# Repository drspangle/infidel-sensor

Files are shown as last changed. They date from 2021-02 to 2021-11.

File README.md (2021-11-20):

# Inline Filament Diameter Estimator, Lowcost (InFiDEL)

<p xmlns:dct="http://purl.org/dc/terms/" xmlns:vcard="http://www.w3.org/2001/vcard-rdf/3.0#">
  <a rel="license"
     href="http://creativecommons.org/publicdomain/zero/1.0/">
    
  </a>
  Originally created by Thomas Sanladerer
</p>

*A cheap, yet precise filament diameter sensor, intended to compensate for filament diameter deviations in real-time.*

The InFiDEL is a cheap (< $5) filament diameter sensor intended for use with FDM 3d printers.
The sensor can be calibrated to provide surprisingly precise filament diameter readings in real-time. 
The main idea is to use the sensor to correct for filament diameter deviations while printing.

Based on this proof-of-concept: https://www.youmagine.com/designs/filament-diameter-sensor

Detailed documention for InFiDEL: https://infidel-sensor.readthedocs.io/

## Assembly and Setup
Assembly and Setup Instructions on Youtube (https://www.youtube.com/watch?v=RYgdLPe_T0c)

### Calibration
- Flash board with calibration.ino
- Connect a host via I2C (see provided host-example.ino)
- Insert each calibration drill bit shafts and replace the lookup table entries in driver.ino with your own measurements
  * Measure the actual diameter of the shafts and fill second column
  * Use the host's output *1000 to fill first column
- Finally, flash driver.ino with your values filled out
- Hub should now output exact diameter values

#### Note:
Analog output is currently not enabled in driver.ino (I2C and FAULT pin only)

## BOM

### Printed Parts
1 Block
1 Lever

#### Note:
Parts should preferably be printed in PETG, ABS or ASA as PLA may creep significantly over time.

### Electronics
There are two board variants included in this repository, either can be used to assemble the InFiDEL. 
PCBs and electronic components can be easily ordered via the [Kitspace project page](https://kitspace.org/boards/github.com/drspangle/infidel-sensor/) as it can auto-fill carts and get pricing on PCBs and electronic components from common suppliers.

Choose one:
- SMT control board (which is populated; Gerber files and component specifications are included) 
- THT control board

Also required:

- Suitable programmer for ATTiny85 (eg USBtinyISP)
- 1 SS495A linear hall effect sensor (or comparable)

### Fasteners
- 2 M3x8 screws (eg ISO 4762 M3x8)
- 1 3x24mm pin (eg DIN 7 3x24mm, for mating lever to the block)
- 1 3x16mm pin (eg DIN 7 3x16mm, for roller bearing in lever)
- 1 3x18mm pin (eg DIN 7 3x18mm, for idler bearing in block)
- 6 M3 threaded inserts
- 1 M6x5 or M6x8 grub screw (eg ISO 4026 M6x5, for pre loading spring) 

Pins may be replaced with screws or grubscrews, which may result in decreased precision.

### Other Hardware
- 1 6x2mm magnet (eg N35)
- 4 623 bearings (preferably 623-2Z / 623-ZZ)
- 1 Ballpoint pen spring (or other soft 4mm spring)
- Short length of PTFE tube

### Calibration Accessories
- 1 1.5mm drill bit
- 1 1.7mm or 1.8mm drill bit 
- 1 2mm drill bit
- Calipers for verifying drill bit shaft diameter

Drill bits may be replaced with similar diameters. 
Measured diameter is to be written to firmware lookup table.

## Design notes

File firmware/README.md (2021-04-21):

# Inline Filament Diameter Estimator, Lowcost (InFiDEL) - Firmware

<p xmlns:dct="http://purl.org/dc/terms/" xmlns:vcard="http://www.w3.org/2001/vcard-rdf/3.0#">
  <a rel="license"
     href="http://creativecommons.org/publicdomain/zero/1.0/">
    
  </a>
  Originally created by Thomas Sanladerer
</p>

## Files
| File | Note |
| --- | --- |
| calibration.ino | First test firmware by Thomas Sanladerer, it sends the ADC raw value over I2C, insert some drills of known diameters into the sensor and note the ADC value, then put the values into driver.ino and re compile |
| driver.ino | Code for the sensor, it uses a hardcoded table to convert the ADC to Diameter, and sends 2 bytes over I2C -- no analog out |
| host-example.ino | Reads  the 2 bytes of diameter over I2C, and displays it over the UART, used to test the sensor |
| Host_ee_prog.ino | Code for the Host Arduino, uses bidirectional communication with the sensor and has a simple UART Console to do the calibration and sensor testing |
| Infidel_release_ee.ino | Firmware for the sensor, table in EEPROM, sets values over I2C |

## Setup and Programming 

### Requirements
- Arduino > V1.8.8
- TinyWireS LIbary from https://github.com/nadavmatalon/TinyWireS
- ATtiny85 Board for Arduino from https://github.com/damellis/attiny
- ISP Programmer like Arduino over ISP --> https://www.arduino.cc/en/Tutorial/BuiltInExamples/ArduinoISP
 
Load the code, wire the ISP program to the ISP port on the sensor and program it.

Remember to set the processor to Attiny85.

Tools --> Processor: Attiny85

Tools --> Clock: Internal 1 MHz

Tools --> Burn bootloader to set the fuses

Sketch --> Upload with Programmer

After programming, the LED should flash two times.

## Wiring to the Host Board

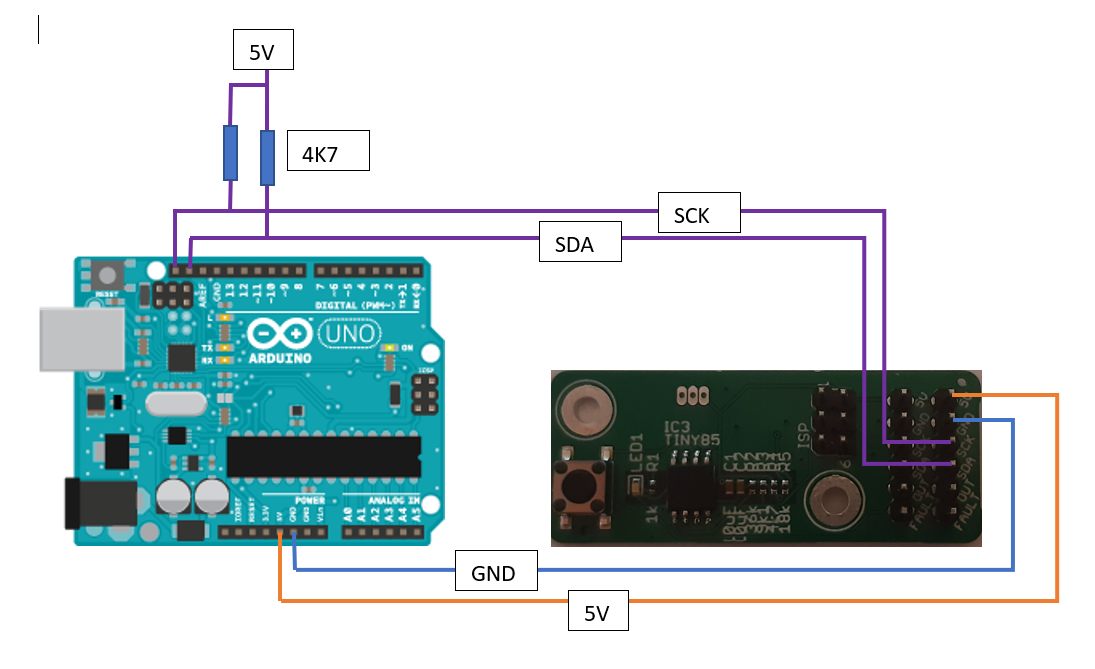
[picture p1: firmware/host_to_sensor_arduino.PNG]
Wire Diagram


Connect the the sensor to the host board, such as an Arduino Uno or Mega.

Program the Host with Host_ee_prog.ino and start the console with 19200 baudrate.

## Console

On start, the following is shown:
```sh
Infidel Sensor Programmer
Scanning...
I2C device found at address 43 
 
Version: 3.12
Table [ADC] [DIA in um]:
00: 0000 / 3000
01: 0619 / 2090
02: 0702 / 1700
03: 0817 / 1400
04: 1000 / 1000
05: 1023 / 0000
Table [DAC min Uout in uV] [DAC max Uout in uV]:
09: 1344 / 2017
Command Input 0 - val / 1 - RAW val / 2 - Version / 3 - Table / 4 - Set Tabel Val / 5 - Ongoing raw read / 6 - sample Mean ADC Val
Command Input 7 - DAC 0 PWW / 8 - DAC 255 PWM

```

| Commands | Note |  Output |
| --- | --- |  --- |
| 0 | Read the Diameter value  |  Diameter [mm]: 2.242 |
| 1 | Read the Diameter + raw ADC Value | Diameter [mm] / [ADC]: 2.242 / RAW: 515 |
| 2 | Read the Version | Version: 1.11 |
| 3 | Read the Diameter Table | Table [idx] [ADC] [DIA in um] |
| 4 | Set the Value in the Table | Input values for Table [IDX],[ADC],[DIA um] like (1,619,2090) |
| 5 | Ongoing reading the ADC raw Value, stop when the command 5 is sent one more time | 
| 6 | Read Meanvalue from Sensor (100 Samples), Display Min / Max / Mean / cnt, used it for Calibration | ADC Mean: 704 / Min: 688 / Max: 713 / Cnt: 100 |
| 7 | Set DAC to PWM 0 --> for check Output Voltage at LOW |
| 8 | Set DAC to PWM 255 --> for check Output Voltage at HIGH |
| h | Show the command list |

## Calibration

Start with the bigger shaft of known diameter (e.g., 2 mm), insert it into the sensor and read the raw ADC value with command "6".
Command "6" determines the mean value over 100 measurements and removes the outliers

```sh
ADC Mean: 704 / Min: 688 / Max: 713 / Cnt: 100
```
Note the ADC value and use the command "4".
The console should show:

```sh
Input values for Table [IDX],[ADC],[DIA um] like (1,619,2090)
Input: 
```

Input this string: `1,503,2000`
Means, Table Index 1 (Command "3"), ADC Val 503, Diameter 3

Repeat this for the next two Ddiameter (1,7mm, 1,4 mm) and write the values to the sensor.

At the end check the settings with Command "3".

```sh
Table [ADC] [DIA in um]:
00: 0001 / 2999
01: 0617 / 2092
02: 0722 / 1711
03: 0816 / 1401
04: 0999 / 1001
05: 1022 / 0001
```

The values are stored in the EEPROM and will load from the EEPROM at the next power up.

If you program the sensor with a new firmware over the ISP the EEPROM will be erased and the sensor will start with default settings.
 
## Calibration with Button (Standalone)

Press the Button at Powerup for 3 sec, if the Calibrationmode start the LED flashes 10 times
The sensor sends an analog signal to Pin 5 [OUT].

* Step 1, Led Flash 1 Times
	*   Insert Drill with 1,4mm
	*   Wait a short Time, 1-2 sec
	*   Press the Button for 1 sec
	*   The Led light for 2 sec, the Sensor is getting 100 Samples from the ADC 
	*   If the messure is Ok the Led flash fast
	*   Remove the drill an press the Button
*   Step 2 Led flashes 2 Times (1,7mm Drill)
    *   Insert the Drill 1,7mm and repeat Step 1
*   Step 3, Led flash 3 times (2mm Drill)
	*   Insert the Drill with 2mm and repeat Step 1

The Calibration is done

## Analog Output
 
The sensor sends an analog signal to Pin 5 [OUT].

The range goes from 1.42 VDC to 2.14 VDC .
The voltage is the analog for the diameter: 1.73V is equal to 1.73mm diameter.

## Calibrate the Analog Output

Connect a Multimeter to GND and OUT.
The Analog Output depend on the VCC Voltage, so make the Calibration when the Sensor is connected to the Printerboard
and not to the unstable USB Port.

* Set with the command "7" the PWM to LOW, meassure the Voltage on Analog OUT and note it (like 1,344 V)
* Set with the command "8" the PWM to HIGH, meassure the Voltage on Analog OUT and note it (like 2,017 V)

Set with the command "4" the table Value for Index 9 (Calibration Values for DAC)
IDX 9 then LOW Voltage and the HIGH Voltage --> like: 9,1344,2017

Check the table with command "3".
The Values are stored in the EEPROM for the next Start

## Fault Pin

The fault pin is high when the diameter is bigger than 3mm and smaller than 1.5mm.
This indicates that the sensor is outside of the normal working range.

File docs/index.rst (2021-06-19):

.. Inline Filament Diameter Estimator, Lowcost (InFiDEL) documentation master file, created by
   sphinx-quickstart on Sat May 15 21:44:02 2021.
   You can adapt this file completely to your liking, but it should at least
   contain the root `toctree` directive.

Welcome to InFiDEL's documentation!
=================================================================================

*A cheap, yet precise filament diameter sensor, intended to compensate for filament diameter deviations in real-time.*

The InFiDEL is a cheap (< $5) filament diameter sensor intended for use with FDM 3d printers.
The sensor can be calibrated to provide surprisingly precise filament diameter readings in real-time.
The main idea is to use the sensor to correct for filament diameter deviations while printing.

Based on this proof-of-concept: https://www.youmagine.com/designs/filament-diameter-sensor

.. toctree::
   :maxdepth: 2
   :caption: Contents:

   license
   bom
   assembly_and_setup

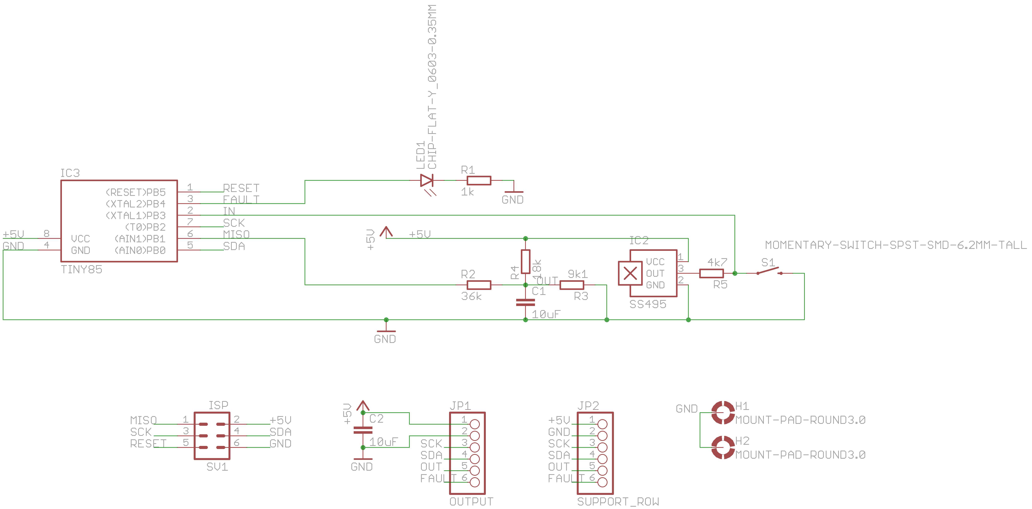
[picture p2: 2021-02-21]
electrical/smt/EAGLE/SMT schematic.png

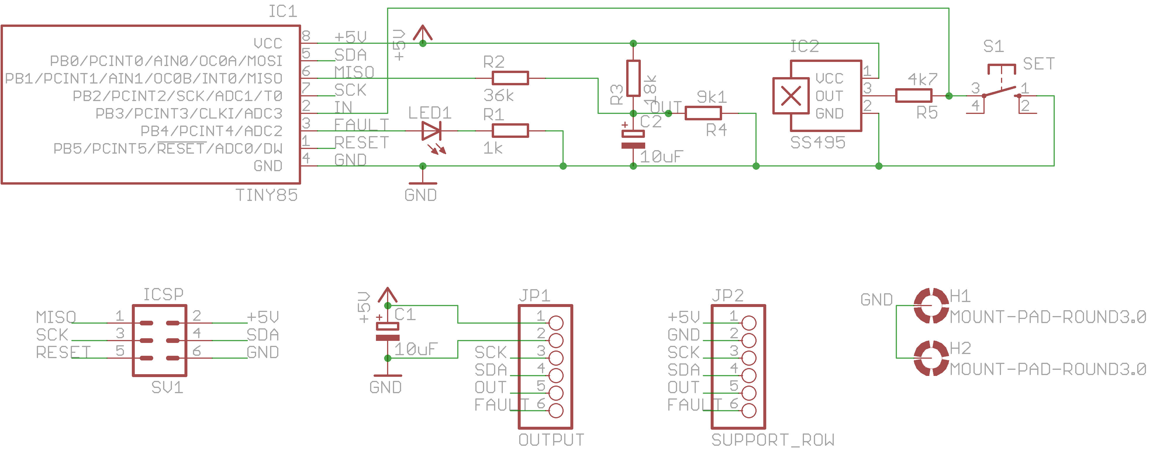
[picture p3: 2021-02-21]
electrical/tht/EAGLE/THT schematic.png

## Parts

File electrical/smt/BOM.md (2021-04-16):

Comment | QTY | Designator | Footprint | Mouser #
--------|-----|------------|-----------|------------
1k Resistor | 1 | R1 | R0402 | [667-ERA-2VEB1001X](https://www.mouser.com/ProductDetail/Panasonic/ERA-2VEB1001X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)
4k7 Resistor| 1 | R5 | R0402 | [667-ERA-2VEB4701X](https://www.mouser.com/ProductDetail/Panasonic/ERA-2VEB4701X?qs=sGAEpiMZZMtlubZbdhIBIFX24rZb7BVEojE2B5%2FPiTs=)
9k1 Resistor|  1 |R3 | R0402 | [667-ERJ-2RHD9101X](https://www.mouser.com/ProductDetail/Panasonic/ERJ-2RHD9101X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)
10uF Capacitor| 2 | C1 C2 | C0402 | [81-GRM155R60J106ME7D](https://www.mouser.com/ProductDetail/Murata-Electronics/GRM155R60J106ME47D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)
18k Resistor|  1 |R4 | R0402 | [667-ERA-2AEB183X](https://www.mouser.com/ProductDetail/Panasonic/ERA-2AEB183X?qs=sGAEpiMZZMtlubZbdhIBILRDuhBknqQkigW4TZMnrhA%3D)
36k Resistor|  1 |R2 | R0402 | [667-ERA-2ARB363X](https://www.mouser.com/ProductDetail/Panasonic/ERA-2ARB363X?qs=sGAEpiMZZMtlubZbdhIBIAI3Iw0L1RezAP9RFTfVAPU%3D)
LED | 1 | LED1 | LEDC1608X35N_FLAT-Y | [604-AA1608SURSK](https://www.mouser.com/ProductDetail/Kingbright/AA1608SURSK?qs=eP2BKZSCXI6pqonvuMmTFg%3D%3D)
Momentary Switch| 1 | S1 | TACTILE_SWITCH_SMD_6.2MM_TALL | [642-ADTSM63NVTR](https://www.mouser.com/ProductDetail/Apem/ADTSM63NVTR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)
ATTINY85 | 1 | IC3 | SOIC8 | [556-ATTINY85V10SU](https://www.mouser.com/ProductDetail/Microchip-Technology-Atmel/ATTINY85V-10SU?qs=8jWQYweyg6NQ5xH6egcL8w%3D%3D)
SS495A Linear Hall Sensor | 1 | - | TO-92-Flat-3 | [785-SS495A](https://www.mouser.com/ProductDetail/Honeywell/SS495A?qs=%2Ffq2y7sSKcKEzWT94S3drA%3D%3D)
ISP PinHeader 2x3 | 1 | ISP | Pin Header | [649-1012938190601BLF](https://www.mouser.de/ProductDetail/Amphenol-FCI/10129381-906001BLF?qs=0lQeLiL1qyZMxGRnx95Mzg%3D%3D)
I2C Header 1x6 | 2 | - | Pin Header | [649-78511-406](https://www.mouser.de/ProductDetail/Amphenol-FCI/78511-406?qs=44C8ns5dLY9MkbPan6dMVA%3D%3D)

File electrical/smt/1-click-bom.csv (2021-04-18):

References | Qty | Description | Mouser
R1 | 1 | 1k Resistor R0402 | 667-ERA-2VEB1001X
R5 | 1 | 4k7 Resistor R0402 | 667-ERA-2VEB4701X
R3 | 1 | 9k1 Resistor R0402 | 667-ERJ-2RHD9101X
C1 C2 | 2 | 10uF Capacitor C0402 | 81-GRM155R60J106ME7D
R4 | 1 | 18k Resistor R0402 | 667-ERA-2AEB183X
R2 | 1 | 36k Resistor R0402 | 667-ERA-2ARB363X
LED1 | 1 | LED LEDC1608X35N_FLAT-Y | 604-AA1608SURSK
S1 | 1 | Momentary Switch TACTILE_SWITCH_SMD_6.2MM_TALL | 642-ADTSM63NVTR
IC3 | 1 | ATTINY85 SOIC8 | 556-ATTINY85V10SU
- | 1 | SS495A Linear Hall Sensor TO-92-Flat-3 | 785-SS495A
ISP | 1 | ISP PinHeader 2x3 Pin Header | 649-1012938190601BLF
- | 2 | I2C Header 1x6 Pin Header | 649-78511-406

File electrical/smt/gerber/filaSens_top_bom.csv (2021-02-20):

Comment | Designator | Footprint | LCSC Part #
1k | R1 | R0402
4k7 | R5 | R0402
9k1 | R3 | R0402
10uF | C1 C2 | C0402
18k | R4 | R0402
36k | R2 | R0402
CHIP-FLAT-Y_0603-0.35MM | LED1 | LEDC1608X35N_FLAT-Y
MOMENTARY-SWITCH-SPST-SMD-6.2MM-TALL | S1 | TACTILE_SWITCH_SMD_6.2MM_TALL
TINY85 | IC3 | SOIC8

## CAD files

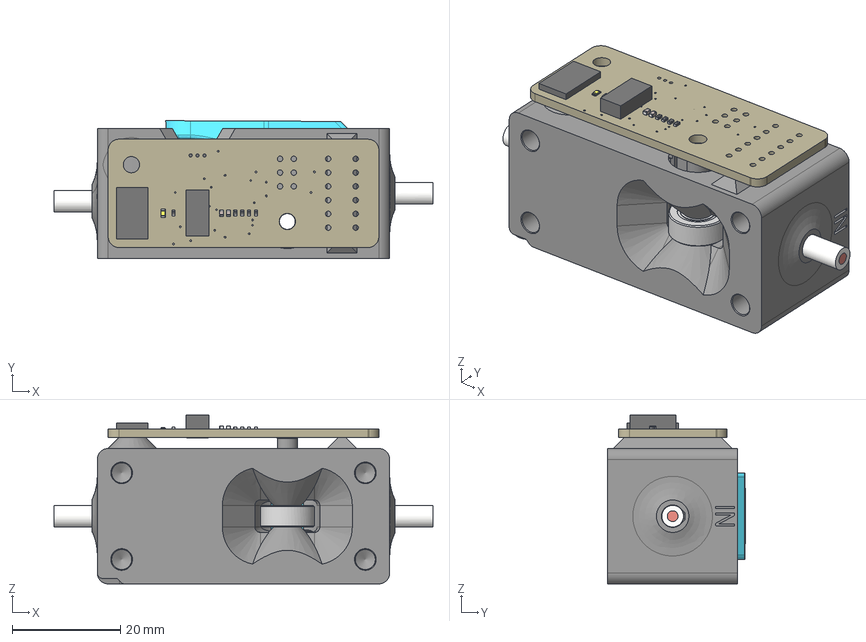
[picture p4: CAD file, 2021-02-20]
mechanical/InFiDEL_release.step
70.0 x 25.4 x 31.2 mm
LeverNew
7804K128 (1)
SpringPlunger
Filament
PTFE (1)
BlockClearance
Board
TACTILE_SWITCH_SMD_6.2MM_TALL
SIP3-UA
SOIC8
C0402 x 2
R0402 x 5

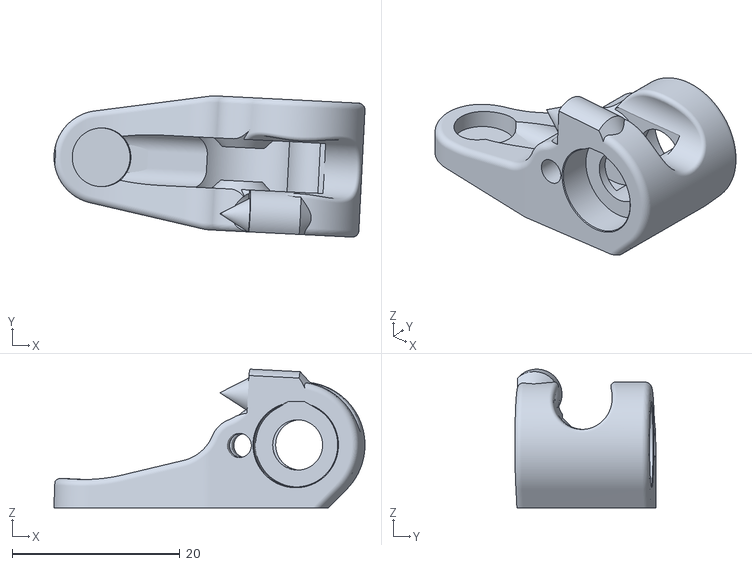
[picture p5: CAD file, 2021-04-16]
mechanical/stl/Lever.stl
37.1 x 16.8 x 16.5

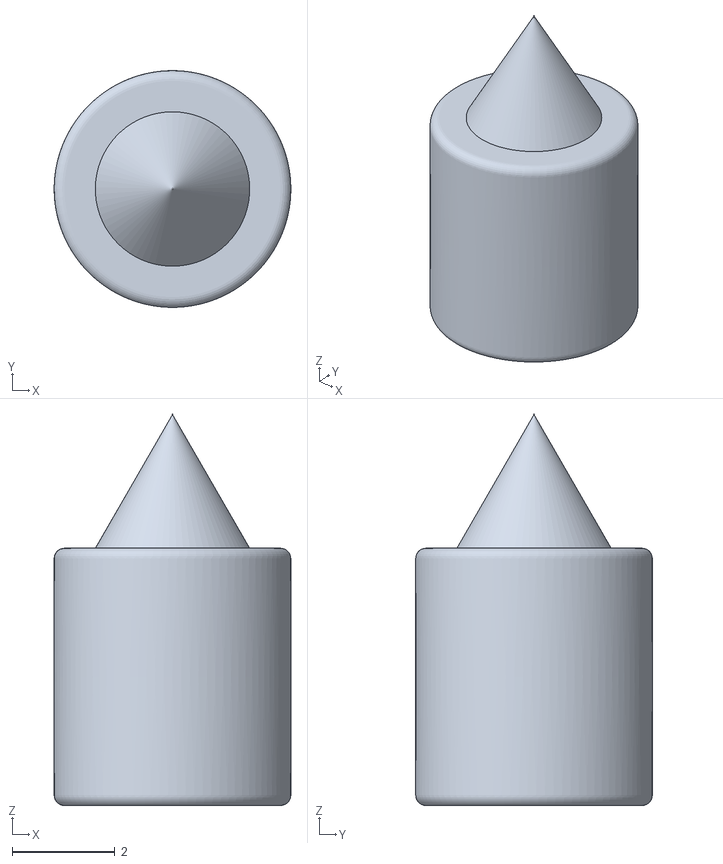
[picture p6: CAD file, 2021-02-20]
mechanical/stl/SpringPlunger.stl
4.60 x 4.60 x 7.60

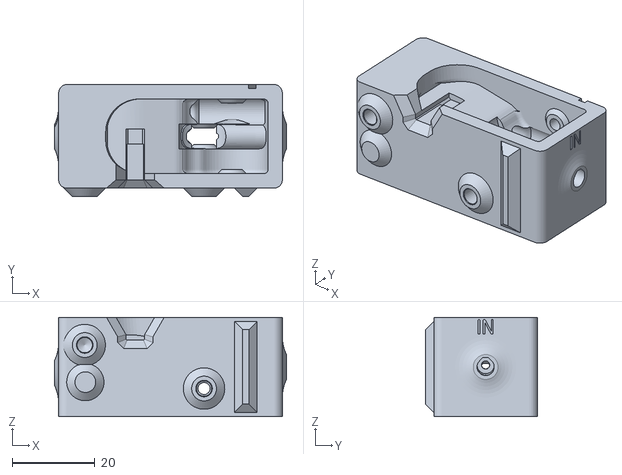
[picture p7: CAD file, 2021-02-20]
mechanical/stl/Block.stl
56.0 x 27.0 x 24.0

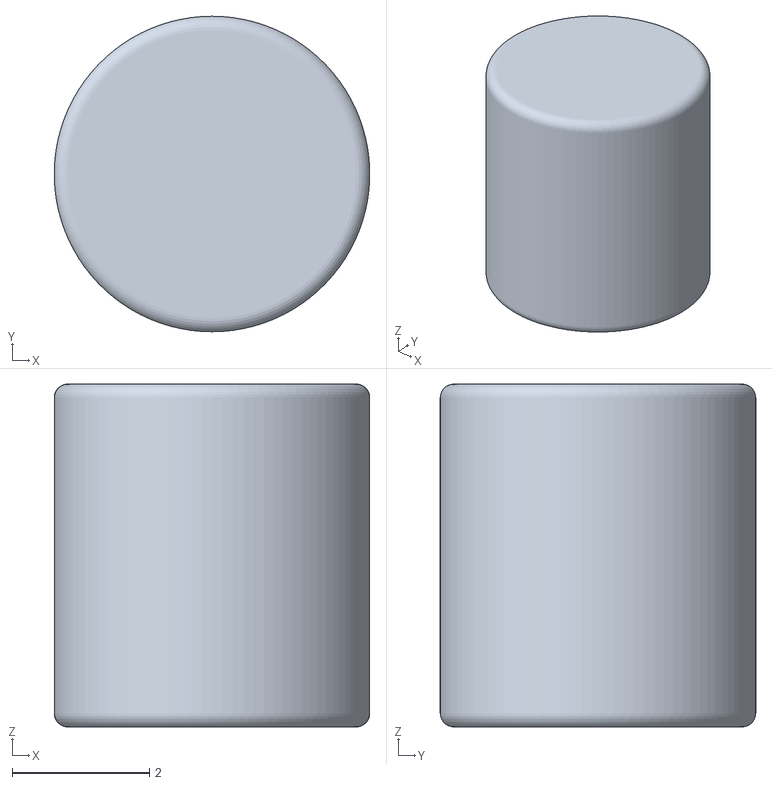
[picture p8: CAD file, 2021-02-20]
mechanical/stl/SpringPlungerExtender.stl
4.60 x 4.60 x 5.00

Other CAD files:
mechanical/LeverDB.f3d

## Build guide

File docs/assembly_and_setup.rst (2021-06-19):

Assembly and setup
==================

Assembly and Setup Instructions on Youtube_

Calibration
-----------
- Flash board with calibration.ino
- Connect a host via I2C (see provided host-example.ino)
- Insert each calibration drill bit shafts and replace the lookup table entries in driver.ino with your own measurements

  * Measure the actual diameter of the shafts and fill second column
  * Use the host's output multiplied by 1000 to fill first column

- Finally, flash driver.ino with your values filled out
- Hub should now output exact diameter values

    Note: Analog output is currently not enabled in driver.ino (I2C and FAULT pin only)


.. _Image: https://www.youtube.com/watch?v=RYgdLPe_T0c

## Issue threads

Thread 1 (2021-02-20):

Choosing an appropriate license

drspangle, 2021-02-20:
It's not clear what license that Thomas Sanladerer intended for this project, he just says it's "all free". We should check to see what he was actually intending -- perhaps it's a CC share-alike license or something.

imitation, 2021-02-20:
"All free" literally means "CC-0 / PD / no rights reserved" in this case. Use in any and every way you deem appropriate - no attribution required (though appreciated).
Allowed use also includes sharing and using any of provided files under a different license.

drspangle, 2021-02-21:
Added LICENSE, fixed in 5d8666c1a287c430bc7336bd76a3391ac569ba7b.

Closed 2021-02-21.

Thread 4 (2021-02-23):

Improve Calibration Procedure - User Feedback

drspangle, 2021-02-23:
Right now, the calibration procedure totally opaque with essentially no user feedback. It would be great if the calibration procedure for the sensor incorporated flashing LEDs to alert the user to the current state of the calibration process. There should be some sort of way to signal the following states:

1. Calibration in progress, insert pin
2. Reinsert pin/retry
3. Calibration stage success, insert next pin
4. Error

Each of the "flash codes" for these states should be documented and the calibration procedure revised.

blurfl, 2021-02-28:
How about adding an I2C display?

drspangle, 2021-02-28:
Nothing wrong with this idea, but it could potentially raise the BOM cost significantly. At the very least, it will require changes to the PCB design and layout. Since calibration shouldn't be happening very often, it might be fine to stick with flash codes for now, since there are only 4 states.

drspangle, 2021-03-05:
It looks like in #8 there was an I2C interface implemented, though I'm not sure how it works and haven't tested it yet. Perhaps there is some potential to do this calibration by connecting to a remote serial console and doing the calibration interactively through that.

blurfl, 2021-03-05:
#8 does set up a serial user interface on the Arduino host, with a 2-way communication to the ATTiny85.

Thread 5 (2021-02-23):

Improve Calibration Procedure - Anomaly Detection

drspangle, 2021-02-23:
Right now, the calibration procedure relies on assumed good measurements for each of the pins of known diameter. A better approach would use repeated measures, then taking the average of these measurements. However, it's possible that erroneous values can creep into the calculations based on the precision of the sensor, and this would drastically affect the operational accuracy. The repeated measures should be combined with a statistical test to ensure that calibration measures are within a certain confidence interval of the likely "population" average, and if they aren't, they should be rejected.

This issue ties in with #4 as it will be necessary to incorporate user feedback in order for the state of the system to be apparent to the user.

The theory of operation and statistical test(s) used should be documented.

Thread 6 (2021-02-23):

Real-Time Measurement Error and Anomaly Detection

drspangle, 2021-02-23:
The micro-controller built in to the sensor has the capability of making the readout smarter than it currently is. While filtering the analog signal from the hall effect sensor certainly helps to minimize the likelihood of extreme outliers with high variance during real-time measurement, it would be nice if there were also built-in tests to determine if there are likely measurement errors or anomalies detected during real-time measurements.

This approach would likely need to rely on certain assumptions, such as the filament being within a certain tolerable spec -- this is likely a safe assumption (using conservative values) as most printers will start to exhibit defective prints in the event that the filament is suddenly out of spec by a huge amount.

The approach to error and anomaly detection is largely dependent on the feed rate (which is unknown to the sensor) and the sensor polling rate (which can be configured).

Errors should be triggered whenever the measurements are (based on statistical tests or otherwise) likely to be far outside the average, perhaps by a configurable threshold (two standard deviations would seem like a very reasonable default). Obviously errors should also be triggered if the filament diameter is detected to be greater than the diameter of the bowden tubes downstream from the sensor (should be configurable), and if the filament is detected to have run out (zero diameter, perhaps over a configurable period of time).

Errors should not be triggered during the following circumstances, as they are the whole point of having the sensor in the first place (assuming otherwise fairly smooth transitions between variances in filament thickness):
- When the filament suddenly gets thicker (as long as it's not so thick there would be a clear problem getting it through the tube), which can happen with filament joiners. This might possibly be an extremely rare condition.
- When the filament suddenly gets thinner (for example, if it has been ground down upstream like in the case of a previous MMU2 loading/unloading failure) the sensor should be capable of detecting this difference and allowing adaptation to the print without failure.

deezums, 2021-03-24:
I agree, and think it might be possible to get the width sensor a feedrate off the signal to the stepper driver. That ought to be able to be used to catch outliers, plus it might be useful for a jam sensor as well.

I've been trying to think of a way to fit a magnetic encoder to the idler bearing, and think tape player pinch rollers might work, around the right size and might be accurate enough to be useful. Although, I think anything I can come up with to fix the idler to the new driven axle shaft would have enough runout to make it unusable as an accurate width sensor, or at least requiring some ridiculous mapping or something. You ought to be able to save a print near instantly on a jam then, plus with a little oled you could track usage and other stats.

I might order a few rubber pinch rollers from ali and see if they might shrink fit on a dowel or something and if they are still decently round, if they'd be hard enough to not deform, and if they'd be able to keep traction...

Outside getting a custom one piece axle made, I'm all ears for ideas for a friction driven idler/axle you could attach a magnet to!

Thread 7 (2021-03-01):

Which TinyWireS library to use

blurfl, 2021-03-01:
calibration.ino and driver.ino both use calls to TinyWireS.write() to send data, but I haven't found a version of the TinyWireS library that includes a write() function instead of send(). Is there a particular library version needed here? Changing .write to .send looks proper and compiles, but I'm not able to test that it works properly.

drspangle, 2021-03-02:
I can't say for sure what the correct library is here as I've yet to construct a prototype for testing myself. If you can show that this works with that change, I strongly encourage a PR which I'll accept expeditiously.

midopple, 2021-03-05:
Hi,
i use this TinyWireS libary

https://github.com/nadavmatalon/TinyWireS

drspangle, 2021-03-05:
@blurfl is the library which @midopple linked to the same as the one you attempted to use?

blurfl, 2021-03-05:
Well found, @midopple. I had not seen this library, but it seems very complete and uses the Arduino Write library's write() approach used by the Arduino host (see Host_ee_prog.ino in #8 for instance). It uses the MIT license, not sure how that meshes with the rest of the project - IANAL.
There would be a benefit to adding the library you settle on to this project 😉

drspangle, 2021-04-24:
It seems like we've settled on the one that @midopple is using, at least in the alternate firmware he's got in here. I think this can be closed now.

Closed 2021-04-24.

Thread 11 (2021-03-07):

JLCPCB makes it look like the pick and place locations are incorrect in the current CPL file

darraghbr, 2021-03-07:
If you go through the order process with JLCPCB the resulting pick and place locations are incorrect.

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

JLCPCB will still accept the files and it should work properly, they go through a checking process where they will adjust the positions by hand.

drspangle, 2021-03-07:
So is the issue that the pad placement for the IC3 chip and the other SMD component is incorrect, or is there a deeper issue here? I'm not seeing precisely what the issue is. Does this screenshot come from JLCPCB's design checker?

darraghbr, 2021-03-07:
I think it's a JLC issue, I've checked and double checked the positions and it just seems the presence of the switch in the CPL file breaks everything.

blurfl, 2021-03-07:
We shouldn't modify our BOM to work around one vendor's internal issue. They correct for it when they review the order.

midopple, 2021-03-08:
I had the same problem with JLCPCB, after contacting support I was told that this is due to the web preview and is still being checked before the production process.

electrickery, 2021-03-20:
My boards arrives some days ago and the components are all at the right places. Haven't started and programmed the board yet.

coelholm, 2021-04-09:
I saw same issue. It is an issue with JLCPCB web preview. I have tried to correct placement position of each component one by one (It was looking fine), but when I got to the last component, everything looked "misaligned" again, so I decided to use original file and my boards are perfect.

drspangle, 2021-04-16:
It seems like this isn't actually an issue, rather is a problem on JLCPCB's end. I'll close this now.

Closed 2021-04-16.

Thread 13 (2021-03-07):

Holes for heat set inserts incorrect size

darraghbr, 2021-03-07:
Let me preface this with the fact that I've not used heat set inserts, so I don't know how sensitive they are to diameter changes.

The holes in the current design are 3.7 mm diameter with a short countersink out to 4 mm. The manufacturers specs for M3 inserts state the hole should be 4 mm.

Does the current design work fine or should the hole sizes be changed? 0.3 mm is not much but is it the difference between a part cracking or not?

drspangle, 2021-03-07:
This is a valid issue but it depends on the material, and also depends on which kind of heat inserts you use. If you use the cheapo ones which are essentially spool shaped, and if you use a material like PETG, having this extra bit of material can help. With PLA this might not be the case.

I think this would be a good issue to keep around, especially if people have issues with printing or assembly.

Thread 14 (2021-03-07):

No mention of spring pre tensioning hardware

darraghbr, 2021-03-07:
I believe there is a missing item on the hardware BOM, I believe there should be an M5 grub screw or the like to pre load the spring in the body of the sensor.

drspangle, 2021-03-07:
I believe you are correct. Tom originally specified that he used a grub screw in his video but I don't know what was specified. Can you verify that an M5 grub screw works, and if so, can you recommend/specify a specific one?

darraghbr, 2021-03-07:
>
>
> I believe you are correct. Tom originally specified that he used a grub screw in his video but I don't know what was specified. Can you verify that an M5 grub screw works, and if so, can you recommend/specify a specific one?

An M5 grub screw definitely does work, and either of the standard sizes (5 or 8 mm long) will work fine.

drspangle, 2021-03-07:
Great! This should definitely get added to the BOM. If you want to create a PR to add this I will review and accept it expeditiously. Nice catch on this one.

drspangle, 2021-03-07:
Fixed in #16.

Closed 2021-03-07.

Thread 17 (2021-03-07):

Investigate the use of the DRV5053 sensor

darraghbr, 2021-03-07:
In place of the SS495A sensor we could instead use a comparable TI part, namely the DRV5053. Pros of the DRV5053 are it is significantly less expensive (less than half the cost) for a similar spec part, they are pin compatible.

I have prototyped the circuit on a breadboard and tested side by side the SS495A sensor and the DRV5053, below is the waveform generated by the two sensors, the DRV is on the left and the SS495A is on the right, as you can see the output is much higher from the SS495.

The polarity is reversed between the sensors, but in theory you just have to install the magnet in the other way around.

I checked it using a magnet on which I marked a side and offered it up to the 2 sensors.

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

Do people think the lower response and reversal of polarity will be an issue?

Below is the breadboard set up for reference.

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

drspangle, 2021-03-07:
The inverted polarity shouldn't be an issue, but I'm wondering about the response time. Do you have a rough idea of what the expected (reliable) sampling rate would be given the small measurement tolerance?

darraghbr, 2021-03-07:
The SS495A datasheets state a response time of 3 μs and the DRV state a typical of 13 μs and a max of 25 μs. I believe either one is appropriate. In terms of sampling rate I'm not sure, but the DRV sensor has a much more detailed application note around designing RC filters to achieve an appropriate bandwidth.

Ultimately it comes down to the filament, it would be interesting to see what sort of frequencies the variations in filament occur at. Can you detect mains switching frequency in the diameter of filament? Of course it wouldn't be at the same frequency unless your feedrate is the same as the original extruder.... Something to keep me awake at night...

blurfl, 2021-03-08:
The reduced response of the DRV5053 is certainly an issue. We're measuring very small differences in movements of the magnet and the chart makes it look like the SS495A has more than four times the full range.

darraghbr, 2021-03-08:
The sensors are closer to one another than you might think, in terms of linear range the DRV sensor beats the SS495 (only by 6 mT but there we are)

Because we are going through a calibration routine I suspect it won't matter, and because we are in a fairly loosely coupled system (lets face it the extruder of a printer can't respond at the rates we are talking about here) I suspect it's all in the weeds.

  | SS495A | DRV5053OA
-- | -- | --
Limits (mT) | 67 | 73
Linearity (%) | 1 | 1
Sensitivity (mV/mT) | 31.25 | 11
Output delay time (μs) | 3 | 13

blurfl, 2021-03-08:
The sensitivity value of the SS495A is more than three times that of the DRV5030A. That’s a lot. We won’t be affected by the limit, we’re working with a small magnet. Our interest is how much the signal changes for a small change in mT.

drspangle, 2021-03-08:
I must admit that as a software guy, the physics and electrical engineering behind the final determination of whether this change will be a problem is increasingly beyond my expertise. However, I would like to offer two things.

First, maybe it would be worth reaching out to Tom to see if he had considered using this alternative sensor, perhaps he has some knowledge or did some tests on this.

Second, it might be worth considering this change in terms of the maximum sensitivity per time unit, rather than overall sensitivity or maximum frequency of a reliable sample in ideal conditions. If we take this approach, it would be more practical to be able to calculate the maximum detectable deviation for a given feedrate, and we can also determine whether this detectable deviation is within an acceptable spec over a number of observations. This is very much related to what I had in mind for #5.

darraghbr, 2021-03-08:
You say we are working with a small magnet, they are quite potent and are quite close to the sensor. Do you know for a fact that we are within the linear region for the sensor?

darraghbr, 2021-03-08:
There are also other SKUs of the DRV5053, including ones with significantly higher sensitivity, in the realm of 90 mV/mT, but they become saturated at much lower levels.

darraghbr, 2021-03-08:
It would be interesting to see what the raw values shake out to be during the calibration process.

blurfl, 2021-03-08:
Maximum sensitivity per time unit would be a function of sensitivity and output delay time. In a device that
The difference in cost here is very small -  these are not expensive parts. The cost of shipping for either one will  be much more than the cost of the part. The sensor in a sensing circuit isn't the best place to cost engineer.

A bigger cost saving might be to use a RPi pico ($4) instead of the custom PCB. Faster, on-board data storage, serial IO as well as I2C, available without custom manufacture.

drspangle, 2021-03-08:
> A bigger cost saving might be to use a RPi pico ($4) instead of the custom PCB. Faster, on-board data storage, serial IO as well as I2C, available without custom manufacture.

While this is true, this is both a substantial change to the hardware design and also a total redo of the firmware (including a shift to a different development environment and language). I'm not sure whether this is a good idea or not at this stage. There is also the potential for a shortfall in available volume of parts.

All of this is a useful discussion, so let's keep hashing this out until we arrive at a practical answer. The goal is to keep the cost as low as possible, but there is an obvious multi-objective trade-off between cost, manufacturability/availability, and utility. It is totally unclear to me what the impact is on these objectives with each of these proposed changes right now.

blurfl, 2021-03-08:
> a substantial change to the hardware design and also a total redo of the firmware

That's a fact. Probably better as a fork. It does work a treat, though 😁.

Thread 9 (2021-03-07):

The lever part has some thin walls that make it almost unprintable

darraghbr, 2021-03-07:
The walls that the bearings locate to are extraordinarily thin, so thin in fact that they are basically unprintable with a normal FDM printer with a 0.4mm nozzle. Even with a 0.25mm nozzle I don't think these details are resolvable in a suitable material ASA, PETG as specified by the original designer.

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

Whereas the solid part should look like:

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

Looking in the CAD the inner and outer faces appear to be intersecting, which will absolutely make any printer sad, as it's trying to print something that is infinitely thin.

drspangle, 2021-03-07:
Is there any likelihood that this was done on purpose?

deezums, 2021-03-24:
The closer the fulcrum is to the fixed pivot the larger the movement at the end of the lever, in other words it's probably on purpose. Nothing about that is unprintable, nor would it be mechanically unsound.  Both bearings and the axle have plenty of material constraining them.

darraghbr, 2021-03-24:
That is not at all what we are talking about or what I have changed in the linked PR.

drspangle, 2021-03-24:
@darraghbr I apologize for the confusion, could you help everyone understand a little better what you are trying to address, versus what @deezums has raised?

darraghbr, 2021-03-24:
In the original CAD there is an infinitely thin wall behind the upper part of the bearing seat, which no printer will be able to produce, leading to the enormous holes that you seen in the preview at the top of this issue. So the first thing I did was make it so there is actual material that sits behind the bearing.

The other thing I did was reduce the chamfer on the hole for the bearing, because as you can see in the original CAD the chamfer intersects with the hole for the axle pin and there is an increased likelihood during assembly of the axle breaking out through the thin wall and rendering the print useless.

drspangle, 2021-03-24:
@darraghbr Okay, thanks for explaining that.

So it seems there are two issues addressed here, the first being a cosmetic issue that affects slicers but perhaps less dramatic of an effect on the overall print. The second issue is improving the fitment for the axle. There should not be much of an effect on the overall positioning of the axle or the attached lever arm from these changes. Have I got that right?

darraghbr, 2021-03-25:
The first issue is not just cosmetic, it gives the bearing a better seat and means the bearing is supported all the way around it's circumference, rather than just the lower 2/3rds.

drspangle, 2021-04-16:
This has been resolved in #10.

Closed 2021-04-16.

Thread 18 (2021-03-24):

Add Electronics BOM

lost-hope, 2021-03-24:
Hello,

would people be interested in electronic BOMs for both PCB versions?
I made a BOM for my build and could add it here and maybe add links to electronic resellers like mouser or similar (EU and US)

drspangle, 2021-03-24:
I assume you're referring to your fork based on pi nano? If that's correct, then I think there are some tough questions that need to be considered about how we can properly version both of these simultaneously, and it may be more suitable to have the pi nano as a separate project, or to pull in limited revisions from a particular branch of the main project.

If you're talking about something else, some more details would be great. In any case, having links to recommended resellers serving a variety of geographic areas would be great; EU (not sure what to recommend here, Amazon perhaps?), North America (Mouser, DigiKey, Amazon, etc.), and Asia (AliExpress) ideally.

blurfl, 2021-03-24:
Having a text BOM for the thru-hole version as well as one for the smt version that is separate from  'electrical/smt/gerber/filasense_top_bom.csv' would be a good thing. That file is in a format specific to ordering from JLCPCB, and I think it should be left as is.
 Better still might be to roll the BOMs and the schematics into an .md file to provide an overview independent of Eagle CAD.

I'me the guilty party who mentioned the rpi pico fork, it really does belong in a separate project or branch.

lost-hope, 2021-03-24:
I have started working on a BOM as a MD file. Currently I included Mouser as a vendor, cause they cover EU and US.
https://github.com/lost-hope/infidel-sensor/blob/main/electrical/smt/BOM.md
@drspangle this is what i mean. A table with the electrical materials listed.

@blurfl what do you want to do with the rpi pico? having a standalone sensor?

blurfl, 2021-03-24:
`rpi pico? having a standalone sensor?`
That, and a cheaper build cost. The power supply seems _very_ noisy, though.

darigovresearch, 2021-04-10:
[Kitspace](https://kitspace.org/) may be the best user friendly implementation of a BOM to resolve the sourcing of electrical components of this project. May be worth checking which suppliers are available and crowd sourcing from the users here who know the catalogues of those suppliers best. Would suggest an initial BOM to be confirmed from one source of parts if the maintainers choose to implement it.

See feature request #19 for more details

drspangle, 2021-04-16:
@lost-hope If you want to make a PR to incorporate your BOM, please do so and I'll make sure it gets reviewed.

lost-hope, 2021-04-16:
I opened PR #20 with the current state and only one vendor (Mouser), cause they seem to ship in both US and EU. Though the shipping cost are quite hight

darigovresearch, 2021-04-17:
I think the pull request resolves this issue, separate issues can be opened for the other vendors to see if anyone else in the community wishes to contribute part numbers for those vendors.

drspangle, 2021-04-24:
This seems to be addressed adequately for now. We'll track the addition of other suppliers in #32 .

Closed 2021-04-24.

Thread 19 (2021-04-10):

[FEATURE REQUEST] Add Kitspace one click pricing

darigovresearch, 2021-04-10:
[Kitspace](https://kitspace.org/) is a project that really helps with building open source hardware as it allows you to (when properly implemented) have an almost one click pricing for the PCB and electronics components. If setup by the maintainers it would really decrease uncertainty if the components chosen are the ones that work reliably.

We haven't had to implement it yet but it seems relatively straightforward to implement and lets users have self-autonomy to replicate the work, build upon it and put it in the hands of users.

Examples of very good implementations of this are the [Open book](https://kitspace.org/boards/github.com/joeycastillo/the-open-book/open-book/) and [ebook wing](https://kitspace.org/boards/github.com/joeycastillo/the-open-book/ebook-wing/) projects by @joeycastillo

https://kitspace.org/1-click-bom/
https://github.com/kitspace/1clickBOM#readme

Would also resolve issue #18 as well

drspangle, 2021-04-16:
What is required to do this?

drspangle, 2021-04-16:
@darigovresearch If you want to set this up and create a PR, I will review it.

darigovresearch, 2021-04-17:
Thanks @drspangle, pull request #23 should contain the files that are required for this repository

drspangle, 2021-04-18:
Addressed in #23.

kasbah, 2021-04-19:
It's up! https://kitspace.org/boards/github.com/drspangle/infidel-sensor/

Closed 2021-04-18.

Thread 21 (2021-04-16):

Wrong size grubscrew

lost-hope, 2021-04-16:
While assembling i noticed that the m5 grub screw is too small. So i looked into the Fusion files. It is a M6 screw needed. Can you please change that (Making a fork and a PR is too much for a simple textchange imo)

drspangle, 2021-04-16:
I'll make the change.

drspangle, 2021-04-16:
Fixed in #22

Closed 2021-04-16.

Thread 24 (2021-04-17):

[FEATURE REQUEST] KiCad version of PCB

darigovresearch, 2021-04-17:
We may get more contributions/improvements to the system if it is in an open source PCB format like KiCad as it would reduce the barrier to entry for new users. Was wondering if the maintainers or someone from the community would be interested in trying this out.

https://www.kicad.org/

midopple, 2021-04-17:
I have add the KiCad Files for the SMT Version, see Pul request #26

darigovresearch, 2021-04-17:
@midopple thanks for taking the time to do this, have managed to see if we can open the files & it seems to be working. Unsure if the porting has resulted in any differences from the original as we're still relatively new to PCB design & KiCad

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

drspangle, 2021-04-18:
I can't tell if there are any differences, and this will potentially create issues if both sets of schematics are not updated, but I'm of the opinion that if this helps the project gain traction among the community then it's worth the risk. Addressed in #26.

darigovresearch, 2021-04-24:
@midopple thanks for the pull request & @drspangle thanks for merging it. We also believe that having both copies is worth the risk if it encourages people to join the project. Keeping it updated in KiCad could also be good easy pull requests for people who want to get started in contributing to KiCad projects.

Closed 2021-04-18.

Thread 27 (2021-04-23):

Capacitor grounds not connected

eltobu, 2021-04-23:
As can be seen in the screenshots below, the grounds of the two capacitors are connected to each other and a ground fill island on the bottom side.
This ground fill island is then not connected to the rest of ground, but it should be.
Top side:
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
Bottom side:
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

blurfl, 2021-04-23:
That's a good find. Could you add pics to PR #28 to show the fix?

eltobu, 2021-04-23:
Yeah, would have been a good idea in the first place.
I have added screenshots of the full board and both layers.

darigovresearch, 2021-04-24:
@eltobu good catch, & @blurfl thanks for the fix. Can anyone tell if this issue is also in the KiCad version of the project as it was autogenerated a week before this fix?

drspangle, 2021-04-24:
@darigovresearch As far as I can tell, #28 addressed the problem in the KiCad version, and #29 addressed the problem in the EAGLE version.

darigovresearch, 2021-05-09:
Thanks @drspangle for confirming & @blurfl for the fix!

Closed 2021-04-23.

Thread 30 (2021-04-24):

Add kitspace link to readme

darigovresearch, 2021-04-24:
Now we have an easy way to order PCBs & electronic parts it would be good to make it discoverable from the electronics section of the readme

See below for context
- https://github.com/drspangle/infidel-sensor/issues/19
- https://kitspace.org/boards/github.com/drspangle/infidel-sensor/

darigovresearch, 2021-04-24:
Pull request #31 would resolve this issue if merged

drspangle, 2021-04-24:
This was addressed in #31.

Closed 2021-04-24.

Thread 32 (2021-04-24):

[FEATURE REQUEST] Add remaining Kitspace distributors for electronic components

darigovresearch, 2021-04-24:
As a [Kitspace page](https://kitspace.org/boards/github.com/drspangle/infidel-sensor/) has now been implemented to automatically order parts & get pricing it would be good to get any of the remaining suppliers in order to find best prices. If anyone in the community knows any of these catalogues well it would help get this design into the hands of users to help test and improve the project.

Happy to split this into individual issues to help encourage contributors if the maintainers agree as then it is easier to assign specific retailers to specific users and use this one to track progress overall

Suppliers implemented
- [x] Mouser

Suppliers not yet implemented
- [ ] Digikey
- [ ] Farnell/Element14
- [ ] Newark
- [ ] RS
- [ ] LCSC

drspangle, 2021-04-24:
This should be fine as a single issue. I'll have you be in charge of this one.

darigovresearch, 2021-04-24:
Happy to direct contributors on how it works but may not be sure if the components selected should be vetted by more experienced people with this project to avoid anyone (particularly those new to PCB design) ordering incorrect parts and then being turned off from the project when it doesn't work as expected.

May be good to add the tag `Good first issue` and `Help wanted` tags to this issue to encourage people to take part if possible

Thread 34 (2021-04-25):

[FEATURE REQUEST] Molten plastic version of the sensor

darigovresearch, 2021-04-25:
We know it's not particularly easy to make 3D printer ready filament from recycled material but if the sensor could work on molten extruded filament as well it may unlock with other open source machines like the precious plastic extrusion machine to make dimensionally accurate material - https://preciousplastic.com/solutions/machines/basic

In the video Tom mentions that the current design is not particularly optimised for molten extruded material as the pressure of the spring and bearings are too high and may "ovalise" the filament. What would be needed to be adjusted to the current design for the above use case to be feasible?

Video in question - https://www.youtube.com/watch?v=RYgdLPe_T0c

drspangle, 2021-04-25:
This isn't feasible with this kind of filament sensor design. To measure molten filament requires a solution which doesn't involve putting any sort of pressure on the filament -- optical sensors are the only feasible approach. This is way out of scope for this kind of low cost filament measurement solution.

Closed 2021-04-25.

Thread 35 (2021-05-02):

Can it output analog values from 0-5V

TeslaMaker, 2021-05-02:
im thinking of using this for a filament extruder with the firmware called mackerel
https://github.com/filipmu/Marlin-Mackerel
this accepts 0-5v for the sensor value , is it possible to tweak something here so as to give a pwm signal or analog from 0-5v?

drspangle, 2021-05-02:
I believe that the firmware provided by @midopple already has this capability. See: https://github.com/drspangle/infidel-sensor/blob/main/firmware/README.md#analog-output

You would need to use additional circuitry to boost the gain on this output to within the range you want:

> The range goes from 1.42 VDC to 2.14 VDC . The voltage is the analog for the diameter: 1.73V is equal to 1.73mm diameter.

I believe that this output is created through PWM, as there is no other way I can think of which would be possible to generate this voltage using the facilities on the hardware as-is.

Closed 2021-05-02.

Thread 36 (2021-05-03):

issue with AISLER PCB ordering

nlooije, 2021-05-03:
When ordering PCB on AISLER (accessed through the kitspace website) the PCB apparantly isn't loaded properly:

- PCB, Stencil tabs don't load, are in infinite loop getting production date
- Parts aren't loaded from the BOM

This issue is solved by downloading the Github repo and manually uploading the EAGLE file on AISLER

drspangle, 2021-05-03:
Paging @darigovresearch ...

darigovresearch, 2021-05-03:
@kasbah is this a known issue for AISLER?

kasbah, 2021-05-03:
Thanks for reporting and ating me. Seems to be the same if you download the Gerber zip and upload manually. The Gerbers look OK except the outline doesn't show with Tracespace ([link](https://tracespace.io/view/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)). The outline does show up when using Gerbv. There also seems some copper outside the outline, but I feel like this should still be able to work.

Maybe @PatrickFranken has some insight why the Aisler preview can't cope with the Gerbers ([download here](https://kitspace.org/boards/github.com/drspangle/infidel-sensor/infidel-sensor-60b6436-gerbers.zip)) but can cope with the Eagle file.

kasbah, 2021-05-03:
Just a note: different gerber viewers render the outline differently.

E.g. OSHPark
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

vs PCBWay (which looks very similar to how Kitspace renders it, they may be using Tracespace as well)
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

PatrickFranken, 2021-05-04:
It looks like this is not a general issue but rather limited to this project. To validate this, I double checked the Gerber files for this project. Please note that our Gerber preview is a bit different to other Gerber viewers as it displays the actual processed manufacturing files compared to others which just render the Gerber files. This also makes it a bit more "critical".
In this case the issue is caused by an indistinguishable, double drawn board outline, see screenshot attached. This makes it impossible to resolve *the correct* milling path for this PCB. As soon as this issue is solved the import should work as expected.
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

darigovresearch, 2021-05-08:
Good catch @PatrickFranken, is there anyone from the maintainers of the repository or the community able to resolve this issue in the eagle & KiCad files?

CCMCAGP, 2021-06-14:
Hi,
Related to this issue, I ordered via Aisler by uploading the EAGLE file manually, which gave this rendering:
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
and I sent the design, but the tests post-manufacturing indicate a big number of opens:
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
 Can anyone indicate to the newbie that I am whether this is expected or not?
 Thank you!

PatrickFranken, 2021-06-14:
We are currently seeing quite a lot of false-positive open connections after electrical test of the PCBs. I assume this is also the case here. As the PCB itself is rather simple I expect the manufacturing to be done properly.

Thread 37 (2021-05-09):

[FEATURE REQUEST] Documentation

darigovresearch, 2021-05-09:
Would be good to have a docs page to help improve adoption of the project such as step-by-step assembly instructions for the build and coding. This would help make the project more accessible for new joiners and help pull from a wider audience for new features etc. Would suggest having it in the same repository if possible so it could be hosted as a GitHub page

Example docs frameworks that can be used:
- Read the docs - https://readthedocs.org/
- Docusaurus - https://docusaurus.io/
- docsy - https://www.docsy.dev/docs/

Example of open source documentation based on some of the above frameworks
Open source pick and place machine - https://docs.indexmachines.io/docs/
Open source machines to recycle plastic - https://community.preciousplastic.com/academy/intro.html

Happy to write content for it if the maintainers think this would be helpful and choose which documentation framework they have a preference for

darigovresearch, 2021-05-15:
Sure happy to have a go, do you @drspangle or any of the other maintainers have any preference on the documentation framework?

drspangle, 2021-05-15:
Nope. I own the repo, and I'm open to anything.

darigovresearch, 2021-05-15:
Sounds good, an initial test build can be found in #38

drspangle, 2021-06-19:
I had to move the documentation into the correct folder so that the github pages URL would work properly, otherwise you get a 404 unless you explicitly add `/html/build/` subfolder in the URL.

drspangle, 2021-06-19:
Still doesn't seem to be working properly, all the static assets' locations don't seem to be defined correctly anymore.

drspangle, 2021-06-19:
Fixed, I forgot to copy over additional files that were required from the sources directory. Documentation is up and looks good. It would be nice if we had a way of automating the generation using jekyll but it's not a huge deal to just update the HTML every time we update the docs.

darigovresearch, 2021-06-19:
Yeah as you wish in terms of moving it to adjust the URL to not need to `/build/html/`.

In terms of automation, have seen on other repositories that it can auto build the docs for the pull request so it can be demoed before merging but also auto building the HTML as well. Have yet to try this out but may be a good new feature request to open

Closed 2021-06-19.

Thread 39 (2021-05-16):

License Query

darigovresearch, 2021-05-16:
In the readme it is stated that the project is under a CC0 design but it also links to a previous project which is under a different license (CC-BY-NC-SA) - https://www.youmagine.com/designs/filament-diameter-sensor

As it is derived from a project with a different license should the source project not also be changed for the CC0 of this project to be valid?

drspangle, 2021-05-16:
Thomas Sanladerer released this under CC0 and I chose to retain that licensing scheme. Refer to the original Youtube video that's in the documentation. I believe Youmagine doesn't support CC0 licensing, but if it does then that should be fixed there.

darigovresearch, 2021-05-16:
Thanks @drspangle for the clarification. Would agree that Thomas Sanladerer released this design under a CC0 from the video and knowing his work in open source he genuinely meant it to be under a CC0. Youmagine does handle CC0 licensing as found [this version of the design](https://www.youmagine.com/designs/infidel-inline-filament-diameter-estimator-lowcost-10-24) in the timeline of the project linked above. Would assume that as the previous project was released 7 years ago the new license hadn't been updated in the original project to match this derivative work.

Closed 2021-05-16.

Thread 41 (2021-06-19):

[FEATURE] Add firmware instructions to documentation

darigovresearch, 2021-06-19:
**Is your feature request related to a problem? Please describe.**
There currently is no instructions/documentation on the firmware as in the folder readme

**Describe the solution you'd like**
Take the content from [here](https://github.com/drspangle/infidel-sensor/tree/main/firmware) and put it in a page of the [documentation](https://drspangle.github.io/infidel-sensor/index.html)

**Describe alternatives you've considered**
Leave it in the readme but having it all in one place would be helpful

**Additional context**
N/A

leonhma, 2021-07-11:
made #54 to reflect latest changes

darigovresearch, 2021-08-08:
Thanks @leonhma, hopefully the discussion in https://github.com/drspangle/infidel-sensor/pull/48 will help move this forwards

leonhma, 2021-08-20:
I made #54 by just converting `firmware.md` and adding it online. (Still has to be merged I think). As #55 noticed, some details don't match up. I think we should merge it first and then figure out some of the wrong details.

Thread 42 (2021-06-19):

[BUG] No link to documentation in readme

darigovresearch, 2021-06-19:
**Describe the bug**
There is no link in the readme to point to the newly generated documentation - https://drspangle.github.io/infidel-sensor/

**To Reproduce**
Steps to reproduce the behavior:
1. Go to [README](https://github.com/drspangle/infidel-sensor)

**Expected behavior**
Have a link in the readme to point to the documentation

**Screenshots**
N/A

**Additional context**
N/A

drspangle, 2021-06-21:
Fixed in #49.

Closed 2021-06-21.

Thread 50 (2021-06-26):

[FEATURE] 2.85mm version

Titi9237, 2021-06-26:
Is there a plan for a 2.85mm version of this sensor ?

drspangle, 2021-06-27:
At the moment, we don't have plans for this. However, there's no reason why it couldn't be created with a few modifications to the 3d printed parts.

darigovresearch, 2021-08-08:
@Titi9237 would you be up for making the adaptations for a 2.85 mm version and making a pull request?

Titi9237, 2021-08-08:
I know what modification are needed and it is on my to-do list but unfortunately I am mainly using FreeCad (Linux) so I need to find a Windows computer to make a "clean" 3D file.

Titi9237, 2021-12-23:
I finally found time to do a very rough job to make it work with 2.85 filament.
Basically, expanding the filament path by 1mm in radius to account for the extra diameter of 2.85 filament. Without major changes, there is no way to include a corresponding PTFE tube. We need two bearings that have a 9mm outer diameter (MR93ZZ) in place of the 10mm outer diameter previously used (625ZZ).

The parts will be printed during the holiday to see if the mechanical dimensions are correct. Adn then I will to order the remaining parts to see if everything is ok.

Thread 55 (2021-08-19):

Make the firmware documentation more explicit

CCMCAGP, 2021-08-19:
I would like to make the doc&gt;firmware.rst document more complete and accessible. Can
someone review it and see whether my initial steps are correct?
As a beginner in electronics, I have been struggling to interprete the firmware instructions, but a research project I’m doing requires this filament sensor so I'll have to make it work, on a printer too!

> ### REQUIREMENTS

-  Arduino > V1.8.8
-  TinyWireS LIbary from https://github.com/nadavmatalon/TinyWireS **Download the .ZIP of this library and upload in Tool>Include Library>Add .ZIP library**
-  ATtiny85 Board for Arduino from https://github.com/damellis/attiny **Load this in Board Manager, more info in** https://www.youtube.com/watch?v=AmpHIHM41Hw&ab_channel=Adio_ -
-   ISP Programmer like Arduino over ISP -->
   https://www.arduino.cc/en/Tutorial/BuiltInExamples/ArduinoISP **Set the Arduino Uno as an Arduino As ISP following same video as above. Upload the example ketch ArduinoISP onto the board, this board is now an ISP programmer and you may need a different board as host.**

> Load the code, wire the ISP program to the ISP port on the sensor and
> program it.

This sentence was very obscure to me, so here's how I interpreted and detailed it.

## How to flash firmware onto the sensor

1. Wire the ISP programmer to the ISP port on the sensor.
I think this is different from the host_to_sensor_arduino.PNG wiring drawing because the ISP port is not occupied. So I tried to find the equivalent functions of each pin  on the ISP port and on the Uno ISP programmer.

Type | Pin #   on ISP  port (Sensor) | Arduino Pin (ISP programmer)
-- | -- | --
MISO | 1 | 12
VCC | 2 | 5V
SCK | 3 | 13
SDA | 4 | 11
RESET | 5 | 10
GND | 6 | GND

2.	In Tools, Set processor to Attiny85, Clock to Internal 16MHz **(current doc says 1MHz but the sensor .ino files all say 16MHz),** Programmer to Arduino as ISP
3.	Tools > Burn Bootloader
4.	Open driver.ino and Sketch>Upload with Programmer

## Current status
At the moment, with this method, three issues arise:
**ISSUE 1.** In the doc Firmware, the LED is said to flash twice. For me, it flashed only once.
**ISSUE 2.** With the driver.ino flashed onto the sensor, when I approach a magnet, no matter what the magnet polarity is, the LED is triggered. I wonder if anyone has the same issue. In the video https://www.youtube.com/watch?v=RYgdLPe_T0c&t=14s&ab_channel=ThomasSanladerer (5:19), the sensor should not be triggered with one of the two magnet faces (and that's the direction you should use to stick on the lever). I have a N45 magnet instead of the N35, but I also have the same problem with a much smaller N45 magnet which should have a smaller force.

**ISSUE 3.**  With the current state of the documentation, I don't understand when the 5 different firmwares should be used. Could someone clarify the difference between all these firmware in the description and state exactly on which occasion they should be used?

**TLDR;**

a noob tries to clarify the documentation on the firmware. Can you review up to this stage, and clarify what firmware should be on host and sensor at every step?

PS: I realize this might belongs more to a forum than to GitHub but since I'm not aware of one, please forgive me for posting it here. I hope that maybe my remarks and questions could help to make this project more accessible to others as well.

drspangle, 2021-08-19:
This is a good a venue as any for comments and feedback. I'll take a moment later on today to review this and I'll try and help you out. Other contributors might beat me to it.

leonhma, 2021-08-20:
Doesn't look wrong to me. I can't test it though, my parts are still stuck in China 😬. As you saw, I made a pr (ran firmware.md through a converter and added it to the online docs). I don't really know how detailed this is. @CCMCAGP  you can use the MD document in the `firmware` folder as reference.

CCMCAGP, 2021-08-20:
Thank you for your answers. I realized what is wrong: at this point it is not driver.ino but calibration.ino that should be loaded onto the sensor. Even better to follow along with the firmware.rst doc, these two files are actually not useful as far as I know. To start calibration, you should upload Host_ee_prog.ino onto the Host and Infidel_release_ee onto the sensor. Then you start seeing the next steps according to firmware.rst.
When I'm through with the calibration I will post a more thorough summary!

leonhma, 2021-08-24:
Looks good to me. Feel free to open a PR to my repo and then it can be merged back into this one.

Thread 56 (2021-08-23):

[Bug]: Unexpected behaviour of the sensor ADC to Diameter

CCMCAGP, 2021-08-23:
### What happened?

Sensor is flashed with infidel_release_ee.ino, board with host_ee_prog.ino. This is calibration over I2C.
I have drill bits of different sizes to calibrate with: 1.4, 1.5, 1.6, 1.7, 1.8, 1.9 mm [for my sensor, 2mm doesn't fit at all, 1.9mm doesn't even go all the way in, and 1mm doesn't move the lever].

I expect the normal behaviour of the sensor to be as coded in infidel_release_ee.ino, and indicated in the docs, as shown by orange curve on the graph -> ADC increases with decreasing diameter.

What actually happens with my readings (Command 6)  is the opposite (Blue curve). My ADC readings increase with diameter.

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

Of course this means bad behaviour of the interpolation function `convert2dia` in  infidel_release_ee.ino, so I get incorrect readings when you import the calibrated values in EEPROM starting from the biggest diameter to the smallest, because it includes `if (dia_table[i][0] > in) ...        return (out);       break`.

Another issue is that the ADC range is less wide than expected. The range of ADC values given in firmware.rst is [617,999] for drill bits from 1 to 2mm, for me they are spread out from 26 to 282 for drill bits 1.4 to 1.9mm. The resolution is about 2 (=500/256) values of ADC per micron, it's still ok but I'm wondering whether this shift towards lower ADC values, and slight reduction in range is normal. Probably not...

### Any solutions?

To solve the incorrect readings, I simply flipped the calibration  table so that ADC are sorted in ascending order with the line index of the table.
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

This solved the problem and my readings seem accurate. However I am wondering if I am the only one getting this deviation from the docs or if this is something that should be corrected in the documentation.

### Additional info

I got the unpopulated PCB from Aisler, not altering anything from the SMT files there. Also got the BOM from Kitspace without deviations.

leonhma, 2021-08-30:
I think what happened is that you either inserted the magnet in the wrong direction, or that you calibrated in the wrong order (starting with 1.4 instead of 1.9).

@drspangle what side of the magnet should be pointing towards the sensor? @CCMCAGP you can find this out if you look at the raw readings (`host_ee_prog.ino` should output them, between `0 and 255`). If they are less than 128, that means the south side of the magnet is pointing to the sensor, 128 and higher is north.

I agree there should be clearer instructions and also some examples given in the docs.

drspangle, 2021-08-30:
I'm not actually sure if it even matters what side of the magnet is facing the sensor, but the polarity of the sensor itself definitely matters. That said, I think your hypothesis that the calibration ordering was wrong seems like a much more plausible one than mine now that I think about it.

leonhma, 2021-08-30:
Having the ADC values in ascending order definitely was the right thing to do, before that `convert2dia` shouldn't really have worked (only output the highest value). According to the default table in `infidel_release_ee.ino`, the diameter should get smaller with bigger readings, so I don't really know what's the case here.
@CCMCAGP do you have calipers to measure the filament yourself?

CCMCAGP, 2021-08-30:
Today I'm going to try and remove the lever to put another one with an opposite magnet side. I think that it's being inserted wrongly is the most plausible option. Other thing is, I have a N45 magnet instead of a N35. I would assume that would make the sensor react "better" than worse but then again, I don't know.

I interpreted the instructions in the video as "it doesn't matter which of the 3 pins of the sensor goes where in the PCB, as long as you install the magnet such that the magnet polarity doesn't make the LED light up..." (with calibration.ino flashed on)

As for the diameters, yes I have a caliper, even a micrometer actually, so I'm able to measure the drill bits size accurately. But as I said, I couldn't follow the calibration procedure per say, because the 2mm and 1mm drill bits were either not fitting in or not triggering anything.

leonhma, 2021-08-30:
I don't know about the strength of the magnets but if you get a usable signal it should be fine. The orientation of the sensor does actually matter (`+`, `-`, `O`, in that order, wouldn't want to swap them). Again, if you get a signal, this should be fine. The missing calibration points for 1mm and 2mm don't matter as long as there are enough points to interpolate from. What I suspect is happening with the current calibration table, is that your readings are 'mirrored'. So for example for the reading of `800` it will show the correct diameter of `1659`. From there if the reading decreases, the diameter should increase, since the magnet is further away from the sensor. But according to your table they actually increase. Can you try whether this mirrored behaviour is actually the case? If so, you might be able to just turn the 2nd column in the table upside down (the diameter mappings).

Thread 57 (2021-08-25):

[FEATURE REQUEST]: Add typical changes to be made to a printer firmware

CCMCAGP, 2021-08-25:
One of the main use cases of this project is for filament that is more or less experimental/home-made, and thus varies a lot in diameter, but that you want to print anyway. This filament diameter sensor could be used to allow steady extrusion with varying diameter of filament, especially during a print.

As far as I know there's been no 'complete integration' yet. By complete integration I mean, one or several sensor that would be mounted on a classic Marlin-based printer, like a Prusa MK3S for instance. The sensors (different angles to account for ovality) would send analog readings of the filament diameter to the board, and the firmware would adjust the extrusion steps (maybe with something equivalent to M221 Set flow rate) on the fly, with a delay (i.e. taking into account the speed of extrusion and the distance from reading to extruder, and from extruder to hot end).

I think this needs a number of changes to the printer's firmware, which would be useful to include in this repository too.

I find this feature very interesting myself so I'm ready to spend some time on it, but I would also appreciate the help of someone who's familiar with tweaking things in Marlin. If anyone is interested to collaborate/provide a little support to get this feature faster, please reach out! Thanks.

coelholm, 2021-08-28:
@CCMCAGP, is it not covered by M405 - Filament Width Sensor On?

I remember you can talk to this sensor via I2C, so it is possible to cascade multiple sensors and have one of them reporting average between them. This change should be simple in sensor code, but it would give average between different points of filament. A new design would be required to take 3 measurements at the same point with 120 degree between them. Minimum filament diameter would be 1.443mm, if you use 2.5mm width ball bearings.

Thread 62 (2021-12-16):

[Feature] Filament stuck function

LordPinhead, 2021-12-16:
### Any related problems?

_No response_

### What's your feature?

Could you add a function with an high resolution encoder wheel, to know when filament is stuck? Bigtreetech has something like this with their sensor, but it's really not that reliable:

https://www.youtube.com/watch?v=UUx2R9u6ohE

This review of this sensor shows the problem. If you could add a version, in which one of the bearings is the encoder wheel and add that to the sensor, that would be really a gamechanger. When I look at what you did so far, that can't be that hard.

### Additional context?

None

drspangle, 2021-12-16:
Actually you'd think this is a very simple feature to introduce but it's
shockingly difficult. A primitive version would be to check that the
variance of the filament has not changed beyond a very very small
threshold, but then you'll get false positives when the filament is
actually just very precise. Also, when jamming occurs, the vibration
induced along the filament path from clicking steppers could potentially be
detected as changes in variance. This is a tough problem. Does anyone have
any suggestions that would not require a total redesign or the introduction
of an additional or different sensor? An encoder wheel would do this very
easily for example but that is a  substantial redesign.

On Thu, Dec 16, 2021, 1:16 AM Thomas Behrend ***@***.***>
wrote:

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

LordPinhead, 2021-12-17:
I don't know if you watched the video, this sensor is working somewhat decently, but it has its flaws. But when we think of the problem, what options do we have:

1) Optical sensor: Won't work because the filament would need to have changes in the structure. Optical mice work like that.
2) Mechanical wheel / encoder wheel: Depending on the resolution, this could work. But when you have to completely redo it, that would be not good. We would like to keep the current design and add the functionality.
3) Knocking sensor: Like in a car, the sensor could be on the extruder and fetches "knocking", it should be fine enough for the stepper motors we have to get the jumping of the gears and send it to the board.

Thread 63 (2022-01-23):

compensation of retractions in the calculation of the filament diameter

TamerlanOne, 2022-01-23:
### Any related problems?

I was thinking about the operation of the sensor and as long as it comes to measuring the filament in optimal conditions the system is valid but ... when measuring the filament while printing, a few millimeters of filament will be read 3 times. these multiple reads occur when there are retractions in the gcode. How can we compensate for this error which will be directly proportional to the number and length of the retractions?

### What's your feature?

Compensation of the error due to the multiple reading of the retraction filament

### Additional context?

None

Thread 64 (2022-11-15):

Klipper Support

DennisRoschke, 2022-11-15:
### Any related problems?

I tried to set up the sensor with KLipper as a TSL1401CL filament width sensor, but that only works to a limited extent.
if I have the diameter and Voltage is 1.72 reads kLipper :
Filament dia (measured mm): 2.6415

### What's your feature?

I would be happy about a solution I've been trying for a while but can't find a solution

### Additional context?

None

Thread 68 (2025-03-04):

Correct PCBway BOM parts

Omnipresent77, 2025-03-04:
So I ordered, or tried to, from PCBWay and they asked if I had doubled parts or something. I have no idea how to answer what they were asking.
 I am just going to attach the xls spreadsheet file, and also try to get a gyazo screen shot too.

Also they made it sound like you have to do a minimum of 5. I would just do one if I could.

Also on a different note (rather than open a whole new issue). what would happen if the plastic level, box etc were made of ploycarb instead of petg or abs?

wouldn't having a hall effect potentially near the coils of your hotend motor produce errors maybe?

https://gyazo.com/95154751428e1be52e4f77ed28d33b21

[Quotation --T-3C2W963911A-5sets-1-click-bom(2025-03-04).xls](https://github.com/user-attachments/files/19077982/Quotation.--T-3C2W963911A-5sets-1-click-bom.2025-03-04.xls)

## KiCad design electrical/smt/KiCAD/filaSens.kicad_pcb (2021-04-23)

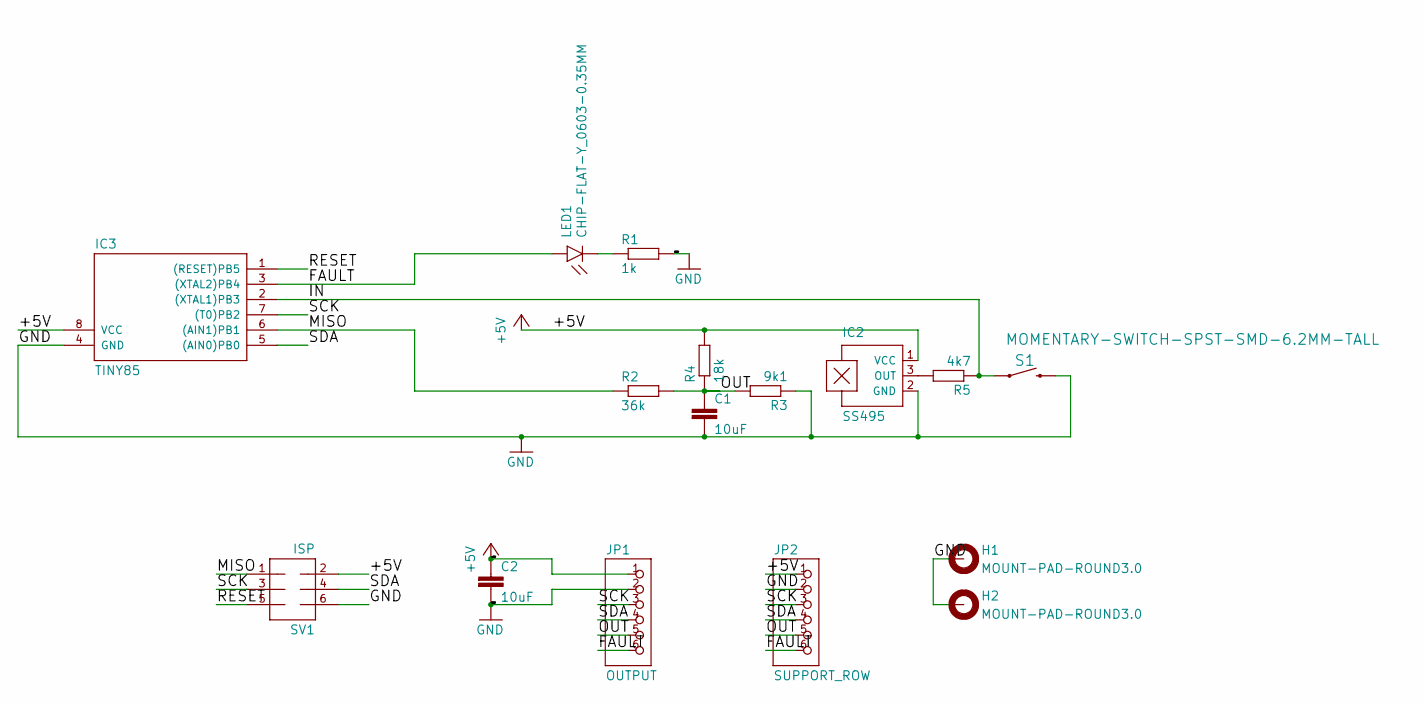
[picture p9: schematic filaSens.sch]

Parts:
C1, C2: 10uF; C0402
H1, H2: MOUNT-PAD-ROUND3.0; 3,0-PAD
IC2: SS495; SIP3-UA
IC3: TINY85; SOIC8
JP1: OUTPUT; 1X06
JP2: SUPPORT_ROW; 1X06
LED1: CHIP-FLAT-Y_0603-0.35MM; LEDC1608X35N_FLAT-Y
R1: 1k; R0402
R2: 36k; R0402
R3: 9k1; R0402
R4: 18k; R0402
R5: 4k7; R0402
S1: MOMENTARY-SWITCH-SPST-SMD-6.2MM-TALL; TACTILE_SWITCH_SMD_6.2MM_TALL
SV1: ISP; MA03-2

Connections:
+5V: C2.1, IC2.1 (VCC), IC3.8 (VCC), JP1.1, JP2.1, R4.2, SV1.2
/FAULT: IC3.3 ((XTAL2)PB4), JP1.6, JP2.6, LED1.A
/IN: IC3.2 ((XTAL1)PB3), R5.1, S1.A2 (1)
/MISO: IC3.6 ((AIN1)PB1), R2.1, SV1.1
/OUT: C1.1, JP1.5, JP2.5, R2.2, R3.2, R4.1
/RESET: IC3.1 ((RESET)PB5), SV1.5
/SCK: IC3.7 ((T0)PB2), JP1.3, JP2.3, SV1.3
/SDA: IC3.5 ((AIN0)PB0), JP1.4, JP2.4, SV1.4
GND: C1.2, C2.2, H1.B3,0, H2.B3,0, IC2.2 (GND), IC3.4 (GND), JP1.2, JP2.2, R1.2, R3.1, S1.B2 (2), SV1.6
unnamed: IC2.3 (OUT), R5.2
unnamed: LED1.C, R1.1

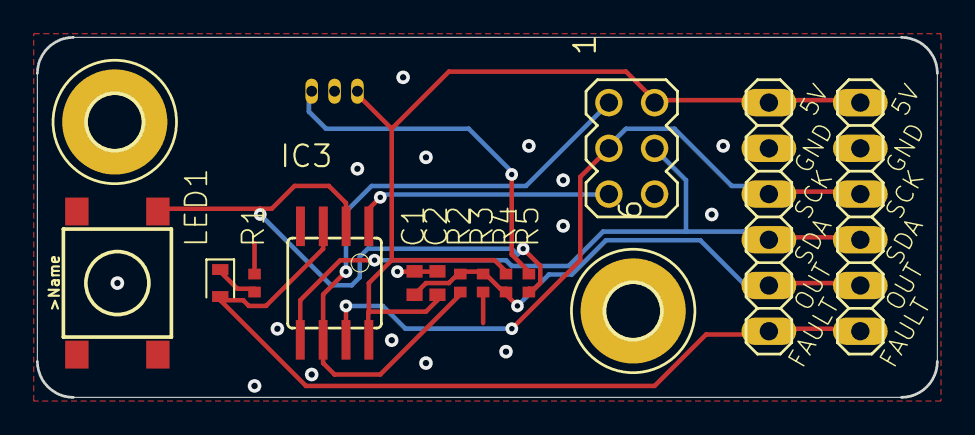
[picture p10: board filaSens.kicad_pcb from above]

Board: 2 copper layers, 50.0 x 20.0 mm, 16 parts (0 on the bottom side), 11 nets.

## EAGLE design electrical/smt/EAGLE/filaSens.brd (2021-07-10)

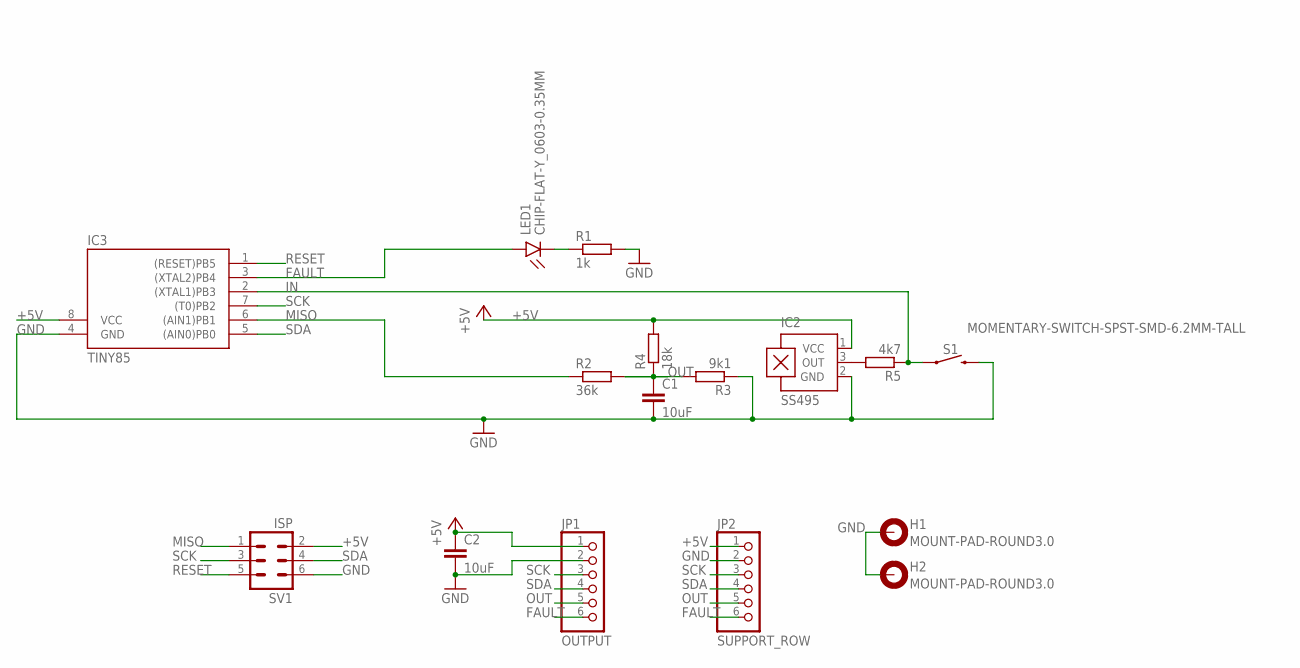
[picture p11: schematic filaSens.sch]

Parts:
C1, C2: 10uF; C0402
H1, H2: MOUNT-PAD-ROUND3.0; 3,0-PAD
IC2: SS495; SIP3-UA
IC3: TINY85; SOIC8
JP1: OUTPUT; 1X06
JP2: SUPPORT_ROW; 1X06
LED1: CHIP-FLAT-Y_0603-0.35MM; LEDC1608X35N_FLAT-Y
R1: 1k; R0402
R2: 36k; R0402
R3: 9k1; R0402
R4: 18k; R0402
R5: 4k7; R0402
S1: MOMENTARY-SWITCH-SPST-SMD-6.2MM-TALL; TACTILE_SWITCH_SMD_6.2MM_TALL
SV1: ISP; MA03-2

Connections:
+5V: C2.1, IC2.1 (VCC), IC3.8 (VCC), JP1.1, JP2.1, R4.2, SV1.2
FAULT: IC3.3 ((XTAL2)PB4), JP1.6, JP2.6, LED1.A
GND: C1.2, C2.2, H1.B3,0, H2.B3,0, IC2.2 (GND), IC3.4 (GND), JP1.2, JP2.2, R1.2, R3.1, S1.B2 (2), SV1.6
IN: IC3.2 ((XTAL1)PB3), R5.1, S1.A2 (1)
MISO: IC3.6 ((AIN1)PB1), R2.1, SV1.1
unnamed: IC2.3 (OUT), R5.2
unnamed: LED1.C, R1.1
OUT: C1.1, JP1.5, JP2.5, R2.2, R3.2, R4.1
RESET: IC3.1 ((RESET)PB5), SV1.5
SCK: IC3.7 ((T0)PB2), JP1.3, JP2.3, SV1.3
SDA: IC3.5 ((AIN0)PB0), JP1.4, JP2.4, SV1.4

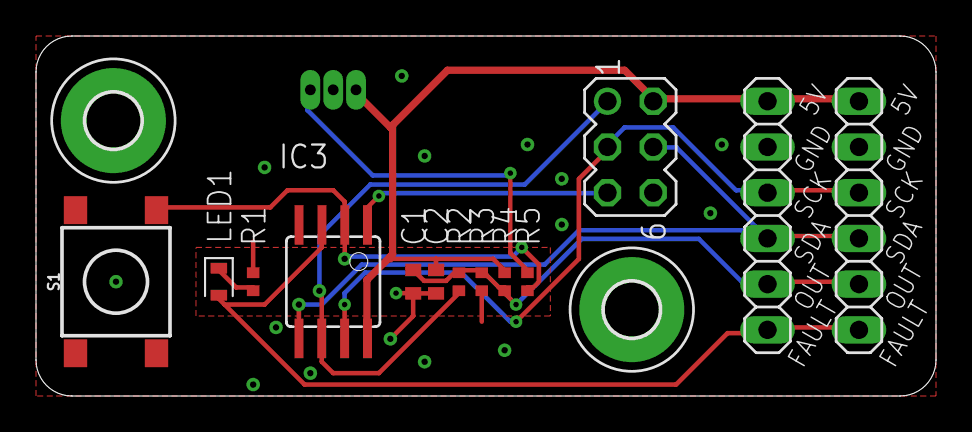
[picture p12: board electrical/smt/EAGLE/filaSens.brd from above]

Board: 2 copper layers, 50.0 x 20.0 mm, 16 parts (1 on the bottom side), 11 nets.

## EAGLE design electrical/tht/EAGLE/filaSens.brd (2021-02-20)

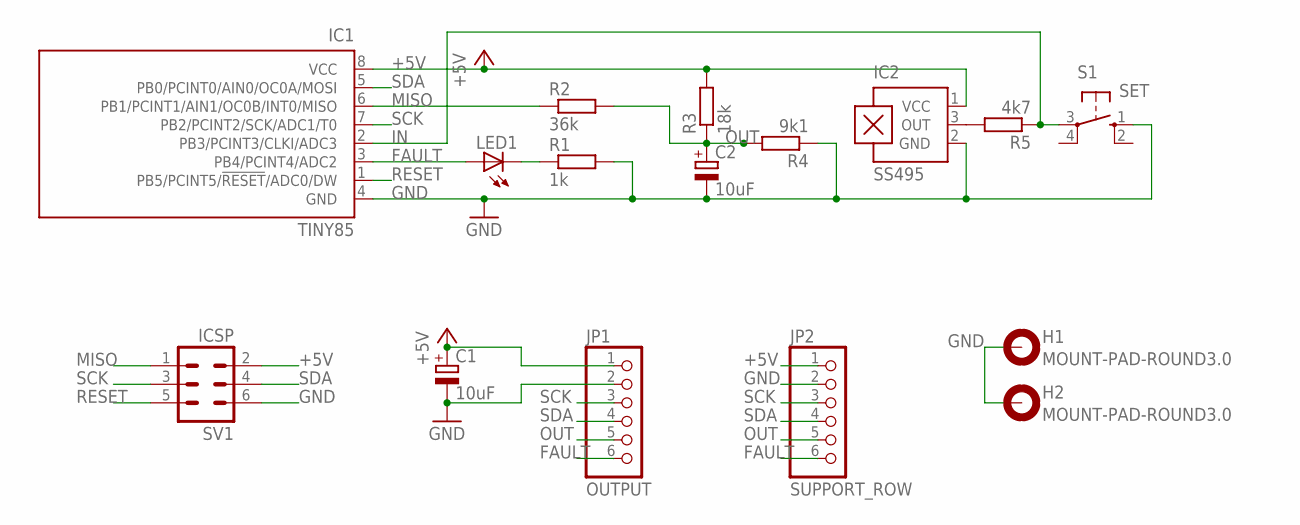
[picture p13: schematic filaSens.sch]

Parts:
C1, C2: 10uF; E2,5-5
H1, H2: MOUNT-PAD-ROUND3.0; 3,0-PAD
IC1: TINY85; DIL08
IC2: SS495; SIP3-UA
JP1: OUTPUT; 1X06
JP2: SUPPORT_ROW; 1X06
LED1: TLLG4400; LED3MM
R1: 1k; 0207/10
R2: 36k; 0207/10
R3: 18k; 0207/10
R4: 9k1; 0207/10
R5: 4k7; 0207/10
S1: SET; B3F-10XX
SV1: ICSP; MA03-2

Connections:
+5V: C1.+, IC1.8 (VCC), IC2.1 (VCC), JP1.1, JP2.1, R3.2, SV1.2
FAULT: IC1.3 (PB4/PCINT4/ADC2), JP1.6, JP2.6, LED1.A
GND: C1.-, C2.-, H1.B3,0, H2.B3,0, IC1.4 (GND), IC2.2 (GND), JP1.2, JP2.2, R1.2, R4.1, S1.1 (S), SV1.6
IN: IC1.2 (PB3/PCINT3/CLKI/ADC3), R5.1, S1.3
MISO: IC1.6 (PB1/PCINT1/AIN1/OC0B/INT0/MISO), R2.1, SV1.1
unnamed: IC2.3 (OUT), R5.2
unnamed: LED1.K (C), R1.1
OUT: C2.+, JP1.5, JP2.5, R2.2, R3.1, R4.2
RESET: IC1.1 (PB5/PCINT5/!RESET!/ADC0/DW), SV1.5
SCK: IC1.7 (PB2/PCINT2/SCK/ADC1/T0), JP1.3, JP2.3, SV1.3
SDA: IC1.5 (PB0/PCINT0/AIN0/OC0A/MOSI), JP1.4, JP2.4, SV1.4

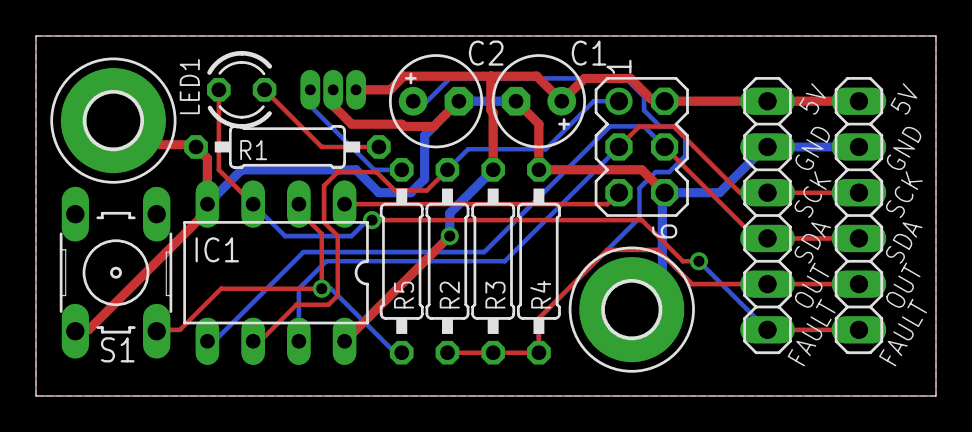
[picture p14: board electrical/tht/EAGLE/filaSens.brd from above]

Board: 2 copper layers, 50.0 x 20.0 mm, 16 parts (1 on the bottom side), 11 nets.

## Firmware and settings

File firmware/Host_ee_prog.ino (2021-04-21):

/*  Firmware for the Host for the (SS495) hall-sensor based filament diameter sensor.
    Reads and send I2C and show Values, 

    Built for Arduino Uno or Mega

    Licensed CC-0 / Public Domain 

    Revised by Michael Doppler (midopple)    
*/


#include <Wire.h>

#define numtemps 6

//Start with sening the Diameter Val, use with Serial Plotter in Arduino
//#define UART_OUT_SCOPE

#define SERIAL_BUFFER_SIZE 32

//I2C addresses for Infidel sensor
#define INFIDELADD 43
//#define INFIDELADD 44 //iterate for additional sensors in same I2C bus

#define I2C_CMD_VAL 0
#define I2C_CMD_RAWVAL 2
#define I2C_CMD_MEANVAL 5
#define I2C_CMD_OVERRIDE_DAC 7
#define I2C_CMD_VER 121
#define I2C_CMD_TABLE 131
#define I2C_CMD_SET_TAB 132

float infidelin = 0;
float infidelin_raw = 0;

short dia_table[numtemps][2];

uint16_t DAC_min_out_voltage = 0;
uint16_t DAC_max_out_voltage = 0;


void setup() {

  Wire.begin();        // join i2c bus (address optional for host)
  Serial.begin(19200);  // start serial for output

  #ifndef UART_OUT_SCOPE
    Serial.println(F("Infidel Sensor Programmer"));

    //Check if the Device at Adress is Online
    check_I2C_adress();

    Serial.println(F("Command Input 0 - val / 1 - RAW val / 2 - Version / 3 - Table / 4 - Set Tabel Val / 5 - Ongoing raw read / 6 - sample Mean ADC Val"));
    Serial.println(F("Command Input 7 - DAC 0 PWW / 8 - DAC 255 PWM"));

  #endif
  
}

void loop() {

  #ifdef UART_OUT_SCOPE
    static uint8_t ongoing_read = 1;
  #else
    static uint8_t ongoing_read = 0;
  #endif
  static uint8_t ongoing_cnt = 0;

  if (Serial.available()) {
    byte inByte_uart = Serial.read();
    switch(inByte_uart){
      case '0':
        readInfidel();
        Serial.print(F("Diameter [mm]: "));
        Serial.println(infidelin, 3);
      break;
      case '1':
        readInfidel_raw();
        Serial.print(F("Diameter [mm] / [ADC]: "));
        Serial.print(infidelin, 3);
        Serial.print(F(" / RAW: "));
        Serial.println(infidelin_raw,0);
      break;
      case '2':
        read_version();
      break;
      case '3':
        read_table();
        print_table();
      break;
      case '4':
        inByte_uart = Serial.read(); //read linefeed from buffer
        get_value_from_uart();
      break;
      case '5':
        if(ongoing_read == 0)
          ongoing_read = 1;
        else
          ongoing_read = 0;
      break;
      case '6':
        readInfidel_mean_val();
      break;
      case '7':
        //Override DAC with PWM 0 for Calibration
        override_DAC_pwm(0);
      break;
      case '8':
        //Override DAC with PWM 255 for Calibration
        override_DAC_pwm(255);
      break;
      case 'h':
      case 'H':
        Serial.println(F("Commands:"));
        Serial.println(F("Command Input 0 - val / 1 - RAW val / 2 - Version / 3 - Table / 4 - Set Tabel Val / 5 - Ongoing raw read / 6 - sample Mean ADC Val"));
        Serial.println(F("Command Input 7 - DAC 0 PWW / 8 - DAC 255 PWM"));
      break;
      case 10:
      break;
      case 13:
      break;
      default:
        Serial.println(F("Error wrong command"));
      break;
    }
  }
  else if(ongoing_read == 1){
    if(ongoing_cnt < 50){
      ongoing_cnt++;
    }
    else{
      ongoing_cnt = 0;
      readInfidel_raw();
      
      #ifdef UART_OUT_SCOPE
        Serial.println(infidelin*1000, 0);
      #else
        Serial.print(F("Diameter [mm] / [ADC]: "));
        Serial.print(infidelin, 3);
        Serial.print(F(" / RAW: "));
        Serial.println(infidelin_raw,0);
      #endif
      
    }
  }
  
  delay(10);
}

void readInfidel() {

  Wire.beginTransmission(INFIDELADD); // transmit to device #44 (0x2c)
  Wire.write(I2C_CMD_VAL);             // sends value byte  
  Wire.endTransmission();     // stop transmitting
  
  Wire.requestFrom(INFIDELADD, 2);
  byte b1 = Wire.read();
  byte b2 = Wire.read();
  infidelin = (((float) b1) * 256 + b2) / 1000;
}

void readInfidel_raw() {
  Wire.beginTransmission(INFIDELADD); // transmit to device #44 (0x2c)
  Wire.write(I2C_CMD_RAWVAL);             // sends value byte  
  Wire.endTransmission();     // stop transmitting
  
  Wire.requestFrom(INFIDELADD, 4);
  byte b1 = Wire.read();
  byte b2 = Wire.read();
  byte b3 = Wire.read();
  byte b4 = Wire.read();
  infidelin = (((float) b1) * 256 + b2) / 1000;
  infidelin_raw = (((short) b3) * 256 + b4);
}

//Sample 100 ADc Val and show min,max,mean,cnt
void readInfidel_mean_val() {
  
  uint16_t minval = 0;
  uint16_t maxval = 0;
  uint16_t meanval = 0;
  uint8_t cntval = 0;
  
  Wire.beginTransmission(INFIDELADD); // transmit to device #44 (0x2c)
  Wire.write(I2C_CMD_MEANVAL);             // sends value byte  
  Wire.endTransmission();     // stop transmitting
  
  Wire.requestFrom(INFIDELADD, 7);
  byte b1 = Wire.read();  //Mean Val
  byte b2 = Wire.read();  //Mean Val
  byte b3 = Wire.read();  //Min Val
  byte b4 = Wire.read();  //Min Val
  byte b5 = Wire.read();  //Max Val
  byte b6 = Wire.read();  //Max Val
  byte b7 = Wire.read();  //CNT

  
  meanval = (((short) b1) * 256 + b2);
  minval  = (((short) b3) * 256 + b4);
  maxval  = (((short) b5) * 256 + b6);
  cntval = b7;

  Serial.print(F("ADC Mean: "));
  Serial.print(meanval, DEC);
  Serial.print(F(" / Min: "));
  Serial.print(minval, DEC);
  Serial.print(F(" / Max: "));
  Serial.print(maxval, DEC);
  Serial.print(F(" / Cnt: "));
  Serial.println(cntval, DEC);

  Wire.beginTransmission(INFIDELADD); // transmit to device #44 (0x2c)
  Wire.write(I2C_CMD_VAL);             // sends value byte  
  Wire.endTransmission();     // stop transmitting
  
}

void read_version(){
  
  Wire.beginTransmission(INFIDELADD); // transmit to device #44 (0x2c)
  Wire.write(I2C_CMD_VER);             // sends value byte  
  Wire.endTransmission();     // stop transmitting

  delay(10);
  
  Wire.requestFrom(INFIDELADD, 2);

  byte b1 = Wire.read();
  byte b2 = Wire.read();

  Serial.print(F("Version: "));
  Serial.print(b1*1, DEC);
  Serial.print(F("."));
  Serial.println(b2*1,DEC);

  Wire.beginTransmission(INFIDELADD); // transmit to device #44 (0x2c)
  Wire.write(I2C_CMD_VAL);             // sends value byte  
  Wire.endTransmission();     // stop transmitting
}


void read_table(){

  byte *tab_ptr;
    
  Wire.beginTransmission(INFIDELADD); // transmit to device #44 (0x2c)
  Wire.write(I2C_CMD_TABLE);             // sends value byte  
  Wire.endTransmission();     // stop transmitting

  delay(10);
  
  Wire.requestFrom(INFIDELADD, 28);

  tab_ptr = (byte*)&dia_table[0][0];
  
  for(byte cnt_i = 0;cnt_i < (numtemps*4);cnt_i++){
    byte b1 = Wire.read();
    *tab_ptr = b1;
    tab_ptr++;
  }

  byte b1 = Wire.read();
  byte b2 = Wire.read();  
  byte b3 = Wire.read();
  byte b4 = Wire.read();
  
  DAC_min_out_voltage = (uint16_t)b1 * 256 + b2;
  DAC_max_out_voltage = (uint16_t)b3 * 256 + b4;

  
  Wire.beginTransmission(INFIDELADD); // transmit to device #44 (0x2c)
  Wire.write(I2C_CMD_VAL);             // sends value byte  
  Wire.endTransmission();     // stop transmitting


}

void print_table(){

  char s[20];
  
  Serial.println(F("Table [ADC] [DIA in um]:"));
  for(byte cnt_t=0;cnt_t < numtemps;cnt_t++){
    sprintf(s,"%02u: %04u / %04u",cnt_t, dia_table[cnt_t][0], dia_table[cnt_t][1]); 
    Serial.println(s); 
  }

  Serial.println(F("Table [DAC min Uout in uV] [DAC max Uout in uV]:"));
  sprintf(s,"%02u: %04u / %04u",9, DAC_min_out_voltage, DAC_max_out_voltage); 
  Serial.println(s);
  
}

void override_DAC_pwm(uint8_t pwm_value){
  
  Wire.beginTransmission(INFIDELADD);  // transmit to device #44 (0x2c)
  Wire.write(I2C_CMD_OVERRIDE_DAC);    // sends value byte  
  Wire.write(10);                       // override is active
  Wire.write(pwm_value);               // PWM Value
  Wire.endTransmission();              // stop transmitting

  Wire.requestFrom(INFIDELADD, 1);
  byte b1 = Wire.read();

  Serial.print(F("SET DAC to: "));Serial.print(pwm_value,DEC);Serial.print(F(" active: "));Serial.println(b1,DEC);

  
  
}


void get_value_from_uart(){

  Serial.println(F("Input values for Table   [IDX],[ADC],[DIA um] like (1,619,2090)"));
  Serial.println(F("Input values for DAC [IDX = 9],[DAC pwm 0],[DAC pwm 255] like (9,1437,2156)"));
  Serial.print(F("Input: "));

  byte uart_in = 0;
  byte index = 0;
  char serialBuffer[SERIAL_BUFFER_SIZE];

  index = 0;
  
  while(uart_in != '\n'){
    if(Serial.available()){
      uart_in = Serial.read();
      Serial.write(uart_in);    //ECHO ??
      if(uart_in >= 32 && index < SERIAL_BUFFER_SIZE - 1)
      {
        serialBuffer[index++] = uart_in;
      }
    }    
  }

  serialBuffer[index] = '\0';

  byte idx      = atoi(strtok(serialBuffer, ","));
  short ADC_val = atoi(strtok(NULL, ","));
  short dia_val = atoi(strtok(NULL, ","));
  byte b1,b2,b3,b4;

  Serial.print(F("read: "));
  Serial.print(idx, DEC);
  Serial.print(F(" / "));
  Serial.print(ADC_val,DEC);
  Serial.print(F(" / "));
  Serial.println(dia_val,DEC);

  if(idx >= 0 && idx < numtemps){
    if(ADC_val >= 0 && ADC_val < 1024 && dia_val >= 0 && dia_val <= 3000)
    {
      b1 = floor(ADC_val / 256);
      b2 = (ADC_val % 256);
      b3 = floor(dia_val / 256);
      b4 = (dia_val % 256);
      
      Wire.beginTransmission(INFIDELADD); // transmit to device #44 (0x2c)
      Wire.write(I2C_CMD_SET_TAB);             // sends value byte  
      Wire.write(idx);             // sends value byte  
      Wire.write(b1);             // sends value byte  
      Wire.write(b2);             // sends value byte  
      Wire.write(b3);             // sends value byte  
      Wire.write(b4);             // sends value byte  
      Wire.endTransmission();     // stop transmitting

      Wire.requestFrom(INFIDELADD, 1);
      b1 = Wire.read();

      Serial.print(F("Set Value for Table. Ack: "));Serial.println(b1,DEC);
    }
    else{
      Serial.println(F("Wrong Value for ADC or DIA"));
    }
  }
  else if(idx == 9){ //Send Values for DAC 
    b1 = floor(ADC_val / 256);
    b2 = (ADC_val % 256);
    b3 = floor(dia_val / 256);
    b4 = (dia_val % 256);
    
    Wire.beginTransmission(INFIDELADD); // transmit to device #44 (0x2c)
    Wire.write(I2C_CMD_SET_TAB);             // sends value byte  
    Wire.write(idx);             // sends value byte  
    Wire.write(b1);             // sends value byte  
    Wire.write(b2);             // sends value byte  
    Wire.write(b3);             // sends value byte  
    Wire.write(b4);             // sends value byte  
    Wire.endTransmission();     // stop transmitting

    Wire.requestFrom(INFIDELADD, 1);
    b1 = Wire.read();

    Serial.print(F("Set Value for DAC Values. Ack: "));Serial.println(b1,DEC);
  }
  else{
    Serial.println(F("Wrong Value for IDX 0-5 or 9"));
  }
  
}


void check_I2C_adress(){
  
  uint8_t I2C_error = 0;
  
  Serial.println(F("Scanning..."));
  Wire.beginTransmission(INFIDELADD);
  I2C_error = Wire.endTransmission();

  if(I2C_error == 0){
    Serial.print(F("I2C device found at address "));Serial.print(INFIDELADD,DEC);Serial.println(F(" "));Serial.println(F(" "));
    read_version();
    read_table();
    print_table();
  }
  else if (I2C_error==1){
    Serial.println(F("data too long to fit in transmit buffer "));
  }
  else if (I2C_error==2){
    Serial.println(F("received NACK on transmit of address  "));
  }
  else if (I2C_error==3){
    Serial.println(F("received NACK on transmit of data  "));
  }
  else if (I2C_error==4){
    Serial.print(F("I2C Error at address / no device found "));Serial.print(INFIDELADD,DEC);Serial.println(F(" "));
  }
}
  

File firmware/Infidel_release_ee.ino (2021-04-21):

/*  Firmware for the **49* (eg SS495) hall-sensor based filament diameter sensor.
    Reads analog value from the sensor and provides a mapped and filtered diameter reading over I2C (optional analog output)

    Built for ATTiny85

    Upload firmware via programmer, using internal 16 MHz clock on ATTiny

    Compact filament sensor hardware and PCB: [URL]

    Licensed CC-0 / Public Domain by Thomas Sanladerer

    EEPROM Update and Value Set over I2C by Michael Doppler (midopple)
    Standalone Calibration from midopple
*/

#include <TinyWireS.h>
#include <EEPROM.h>

//pins as named on PCB
#define FAULT_IO_LED 4 //on-board LED and digital output pin
#define A_IN A3 //SS495 output and push-button input (for calibration procedure)
#define A_OUT 1 //analog (filtered PWM) output, voltage proportional to filament diameter


//I2C
#define I2C_ADDR 43 //iterate for additional sensors in same I2C bus
//#define I2C_ADDR 44 //iterate for additional sensors in same I2C bus

#define smooth 100.0 //intensity of digital lowpass filtering

#define numtemps 6    //Tablecount 

#define VERSION_I2C 12  //I2C Protokoll Version
#define MAIN_VERSION 3

#define EE_CHKSUM_ADR  8

//I2C Commands from Host
#define I2C_CMD_VAL 0
#define I2C_CMD_RAWVAL 2
#define I2C_CMD_MEANVAL 5
#define I2C_CMD_OVERRIDE_DAC 7
#define I2C_CMD_VER 121
#define I2C_CMD_TABLE 131
#define I2C_CMD_SET_TAB 132


float dia = 1.7;
uint16_t  raw_ad_in = 0; //RAW ADC Value for IIC Transmit

uint8_t  I2C_akt_cmd = 0;

//Values for ADC Mean sampling 
uint16_t ADC_mean_min = 0;
uint16_t ADC_mean_max = 0;
uint8_t ADC_mean_cnt = 0;

//Variables for EEPROM handling
uint16_t ee_address = 0;
uint8_t  ee_value;

//Variables for Testing an Calibration DAC Output
uint8_t DAC_override_active = 0;
uint8_t DAC_override_value = 0;
uint16_t DAC_min_out_voltage = 1437;  //DAC out at PWM 0 --> 1,437 V
uint16_t DAC_max_out_voltage = 2156;  //DAC out at PWM 255 --> 2,156 V

int16_t dia_table[numtemps][2] = {
  //{ADC reading in, diameter out [um]}
  //Init Values for the first start
  //After init Values are read from EEPROM
 
  { 0     , 3000 },  // safety
  { 619   , 2090 }, //2mm drill bit
  { 702   , 1700 }, //1.7mm
  { 817   , 1400 }, //1.4mm
  { 1000  , 1000 }, // 1mm
  { 1023  , 0000 } //safety
};



void setup() {
  
  //setup pins
  pinMode(FAULT_IO_LED, OUTPUT);
  pinMode(A_IN, INPUT);
  pinMode(A_OUT, OUTPUT);

  //start I2C
  TinyWireS.begin(I2C_ADDR);
  TinyWireS.onRequest(requestISR);
  TinyWireS.onReceive(receiveISR);

  //blink to indicate sensor powered and ready
  digitalWrite(FAULT_IO_LED, HIGH);
  delay(400);
  digitalWrite(FAULT_IO_LED, LOW);
  delay(400);

  //Check EEPROM Chksum and when OK read Table from EEPROM, 
  //if CHKSUM is not OK write standard Values to EEPROM
  if(read_eeprom_chksum())
    read_eeprom_tab();
  else
    write_eeprom_tab();

  //blink to indicate sensor read EEPROM
  digitalWrite(FAULT_IO_LED, HIGH);
  delay(400);
  digitalWrite(FAULT_IO_LED, LOW);
  delay(400);

  //Check at startup if the Button is pressed to start Calibrazion
  check_for_calibrate();
  
}

void loop() {
  
  //Varibale for Analog Out Calculation
  int16_t aout_val;
  
  //get fresh reading
  int16_t in = analogRead(A_IN);
  

  //Store ADC Value for IIC Transmit
  raw_ad_in = in;
  
  //lowpass filter
  dia += (((float)convert2dia(in)/1000.0) - dia) / smooth;

  //Calculate Voltage for Analog Out --> Volate = Diameter --> 1,73 V = 1,73 mm
  int16_t help_dia_int = (int16_t)(dia*1000);
  aout_val = map(help_dia_int, DAC_min_out_voltage, DAC_max_out_voltage, 0, 255);
  aout_val = constrain(aout_val, 0, 255);
  
  //Write Value to Analog Out
  if(DAC_override_active)
    analogWrite(A_OUT, (uint8_t)(DAC_override_value));
  else
    analogWrite(A_OUT, (uint8_t)(aout_val));

  //light LED and pull up FAULT_IO_LED if sensor saturated, button pressed or diameter low
  if (in < 3 or dia < 1.5) {
    digitalWrite(FAULT_IO_LED, HIGH);
  }
  else {
    digitalWrite(FAULT_IO_LED, LOW);
  }
}


//Send Date over I2C to HOST
void requestISR() {
  
  //sends smoothed diameter reading in um as two bytes via I2C
  //first byte is upper 8 bits, second byte lower 8 bits
  int32_t senddia = 1000 * dia;
  int16_t ADC_help_val;
  uint8_t b1,b2,b3,b4,b5,b6;
  uint8_t *tab_ptr;

  switch(I2C_akt_cmd){
    //Send diameter 2 byte
    case I2C_CMD_VAL:
      b1 = floor(senddia / 256);
      b2 = (senddia % 256);
      
      TinyWireS.write(b1);
      TinyWireS.write(b2);
    break;
    //Send Diameter + RAW ADC for Calibrate 4 byte
    case I2C_CMD_RAWVAL:
      b1 = floor(senddia / 256);
      b2 = (senddia % 256);
      
      b3 = floor(raw_ad_in / 256);
      b4 = (raw_ad_in % 256);
      
      //Send Diameter
      TinyWireS.write(b1);
      TinyWireS.write(b2);
      //Send raw reading for calibration
      TinyWireS.write(b3);
      TinyWireS.write(b4);
    break;
    //Messure Meanvalue for Calibration
    case I2C_CMD_MEANVAL:
      ADC_help_val = sample_AD_cal_val(100);
      b1 = floor(ADC_help_val / 256);
      b2 = (ADC_help_val % 256);
      b3 = floor(ADC_mean_min / 256);
      b4 = (ADC_mean_min % 256);
      b5 = floor(ADC_mean_max / 256);
      b6 = (ADC_mean_max % 256);

      TinyWireS.write(b1);
      TinyWireS.write(b2);
      TinyWireS.write(b3);
      TinyWireS.write(b4);
      TinyWireS.write(b5);
      TinyWireS.write(b6);
      TinyWireS.write(ADC_mean_cnt);
   break;
    //Send version 2 byte
    case I2C_CMD_VER:
      TinyWireS.write(MAIN_VERSION);
      TinyWireS.write(VERSION_I2C);
    break;
    //Response that DAC Override is active
    case I2C_CMD_OVERRIDE_DAC:
       TinyWireS.write(DAC_override_active);
    break;
    // Send Table 24 byte + 4byte DAC cal. Values
    case I2C_CMD_TABLE:
      tab_ptr = (byte*)&dia_table[0][0];
      for(uint8_t cnt_i=0;cnt_i < (numtemps*4);cnt_i++){
         TinyWireS.write(*tab_ptr++);
      }

      b1 = floor(DAC_min_out_voltage / 256);
      b2 = (DAC_min_out_voltage % 256);
      b3 = floor(DAC_max_out_voltage / 256);
      b4 = (DAC_max_out_voltage % 256);

      TinyWireS.write(b1);
      TinyWireS.write(b2);
      TinyWireS.write(b3);
      TinyWireS.write(b4);
    break;
    case I2C_CMD_SET_TAB:
       TinyWireS.write(1);
    break;
  }
}
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

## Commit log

2021-02-20 Update README.md
    Added youtube link for assembly instructions
2021-02-20 add schematic png
    Add png file so Eagle isn't necessary to view the schematic.
2021-03-05 Create Infidel_release_ee.ino
    - Firmware for Sensor with Table in EEPROM
    - Set Table Values over I2C
    - Get Diameter oder RAW Value over I2C
    - Read Table over I2C
2021-03-05 Host Version with I2C Table Programm function
    - Read an write the Table
    - read RAV Value
    - Read Diameter
    - Set Table Valuse over Serial Konsole
2021-03-05 Wire Diagramm Host to Sensor
2021-03-06 Rangecontrol for Input ignore Value 3000, fixed
    [Host_ee_prog.ino]
2021-03-06 Check device on I2C Adress on startup
2021-03-07 Update Lever.stl
    Update Lever.stl to remove infinitely thin walls and generally improve printability
    [Lever.stl]
2021-03-07 Update BOM and CPL so JLCPCB can read it properly
    For some reason when the line for the switch is present in the files the preview of the pick and place locations are incorrect, if you just remove the switch everything seems to work. I do not unders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
    [filaSens_top_bom.csv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]
2021-03-07 Revert "Update BOM and CPL so JLCPCB can read it properly"
    This reverts commit 6b8723a0ccd6b4eb5a09a49f7a27d93d473241ef.
    [filaSens_top_bom.csv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]
2021-03-07 Update README.md
    Corrected M2 to M3 and added details of grub screw for pre loading the spring.
2021-03-08 Create LeverDB.f3d
    Export the modified lever arm, I have called it LeverDB to distinguish it from the original, and there is a small DB inset into the base of the lever.
    [LeverDB.f3d]
2021-03-14 Settings for the attiny and Fuses
2021-03-24 create BOM.md and format the csv into it
    I took the BOM from the Gerber files and reformatted them into a Markdown table
2021-03-24 Fixed LED Mouser Number and added Sensor and Pins
    Removed the ":" in the LED Mouser part number.
    Added The SS495A Sensor
    Added Pin headers for ISP and I2C
2021-04-16 Command "6" for read ADC Meanvalue from Sensor
2021-04-16 Description for Standalnoe Calibration
2021-04-16 Standalone Calibration with Button
    - Standalone Calibration with butten
    - Replace byte to unit8_t, ...
    - Change Delay for 1 Mhz Clock
    - Command I2C_CMD_MEANVAL to send the Meanval over 100 Samples
    - Command 6, to read Meanvalue over 100 Samples with Peak remove for Calibration value
    -If Diameter is smaller then 1,4mm or bigger 2,1mm the Alanogout swap from min to max.
    [Host_ee_prog.ino, Infidel_release_ee.ino]
2021-04-17 command "7" to set the DAC
    - Override the DAC Output for Calibrate the DAC Output
2021-04-17 Opion the Calibrate the DAC Out
    By means of commands "7" and "8" the DAC can be set to LOW and HIGH, the output is measured with a multimeter and the values are stored in the EEPROM.
2021-04-17 feat: Adds initial kitspace code to test
    [1-click-bom.csv]
2021-04-17 fix: Updates title for comment to description in 1-click-bom.csv
    [1-click-bom.csv]
2021-04-17 Add KiCAD Files for SMT Version
    [filaSens.kicad_pcb, filaSens.sch]
2021-04-23 fix capacitor grounds not connected
    [filaSens.kicad_pcb]
2021-04-23 change EAGLE files to capture PR #28 and Issue #27
    change EAGLE files to capture PR #28 and Issue #27
    Update GERBER files as well as EAGLE files
    [filaSens.brd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]
2021-07-01 Fixed cap gnd, made 5v trace larger, re-routed some traces to be cleaner
    [filaSens.brd, filaSens.sch]
2021-08-29 fix: Corrects link to documentation
    Link now points to the readthedocs link https://infidel-sensor.readthedocs.io/, would resolve https://github.com/drspangle/infidel-sensor/issues/60

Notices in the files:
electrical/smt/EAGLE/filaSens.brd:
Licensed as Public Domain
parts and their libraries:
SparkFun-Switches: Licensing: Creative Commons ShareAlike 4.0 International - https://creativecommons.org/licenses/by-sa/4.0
